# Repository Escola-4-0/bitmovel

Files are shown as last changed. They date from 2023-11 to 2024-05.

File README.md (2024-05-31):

# BitMóvel
Com esta placa você pode fazer um robô controlado pela micro:bit que é fácil de montar e programar com a extensão Escola 4.0 para o MakeCode. A própria placa serve como chassi do robô e dispensa o uso de conectores especiais para a micro:bit. A pasta [bitmovel](https://github.com/Escola-4-0/bitmovel/tree/main/bitmovel) contém o projeto da PCB para o KiCAD e arquivos gerber prontos para fabricação.

As peças `para-choque.stl` e `suporte-sensor.stl` podem ser impressas em 3D para caracterizar seu robô e fixar sensores para fazê-lo funcionar como um seguidor de linha. 

## Características da placa (v3)
- Placa em face simples;
- Componentes em PTH para facilicar a montagem manual;
- Fixação da micro:bit usando parafusos;
- Fornece alimentação regulada 3.3V para a micro:bit;
- CI ponte-h para dois motores DC;
- Permite a conexão de sensores para seguidor de linha.

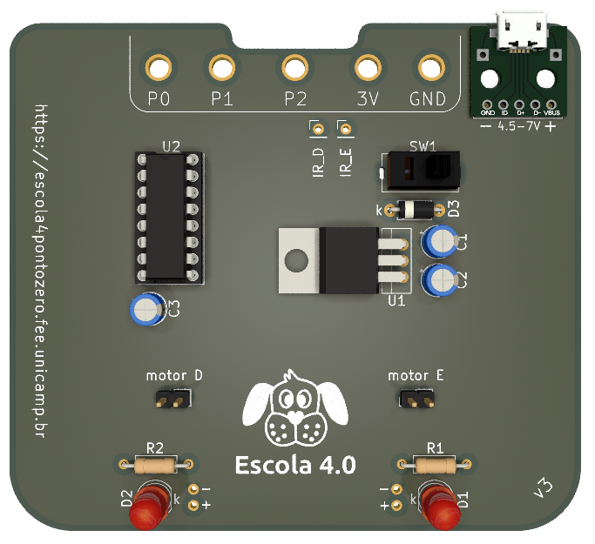
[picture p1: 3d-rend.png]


## Lista de materiais

REF | componente
-- | --
C1 | Capacitor eletrolítico 10uF - 10V |
C2 | Capacitor eletrolítico 10uF - 10V |
C3 | Capacitor eletrolítico 10uF - 10V |
D1 | LED difuso 5mm
D2 | LED difuso 5mm
D3 | Diodo 1N5817 (1N5818 - 1N5822 compatíveis)
J1 | Módulo adaptador micro-USB fêmea para DIP (opcional)
R1 | Resistor 330Ω
R2 | Resistor 330Ω
SW1 | Chave HH SS12F46 - 3 terminais
U1 | LM1117-3.3 (regulador de tensão 3.3V)
U2 | L293D (driver para motor DC)

Para implementar a função de seguidor de linha, são necessários ainda **2 módulos de sensor infravermelho TCRT5000**.

## Descrição e funcionamento
Seis pinos da micro:bit fornecem os sinais de entrada do driver L293D que controla os motores, conforme a tabela: 

pino micro:bit | pino L293D
:--: | :--:
P0 | 2A
P1 | 1A
P2 | 4A
P8 | 1,2EN
P13 | 3A
P15 | 3,4EN

A micro:bit é alimentada pelo regulador LM1117 de 3.3V, o driver L293D e os LEDs são alimentados diretamente pela tensão de entrada, a fonte deve ser de 4.5 a 7V.

Os pinos P14 e P16 recebem os sinais digitais do sensor infravermelho direito e esquerdo, respectivamente.

## Programação
A tabela abaixo resume os comandos para acionamento dos motores:

P8 (P15) | P0 (P2) | P1 (P13) | motor D (motor E)
:--: | :--: | :--: | --
PWM | 1 | 0 | girar horário*
PWM | 0 | 1 | girar anti-horário*
1 | 1 | 1 | parada forçada
1 | 0 | 0 | parada forçada
0 | X | X | parada livre

*O sentido real depende da ligação do motor. X = não importa.

Os sinais dos sensores infravermelho seguem a lógica da tabela abaixo:

P14 (P16) | sensor D (sensor E)
:--: | :--:
0 | luz refletindo, superfície clara
1 | luz não refletindo, superfície escura

No MakeCode, o BitMóvel pode ser programado com os blocos `gravação digital pin` e `gravação analógica pin`, seguindo as combinações da tabela acima, ou com a [extensão Escola 4.0](https://github.com/Escola-4-0/pxt-Escola_4pontozero), usando os blocos da categoria "BitMóvel".

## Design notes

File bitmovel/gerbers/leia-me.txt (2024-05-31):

Cada pasta contém os arquivos em uma versão do formato gerber, X1 ou X2. Verifique com a fabricante qual é o formato compatível.

O projeto contém duas camadas de cobre, mas é possível fabricar a placa em face simples sem perda de funcionalidade, apenas com a camada inferior (bottom layer). Portanto, para fabricar em face simples, ignore os arquivos:
- bitmovel-F_Cu.gbr
- bitmovel-F_Mask.gbr
- bitmovel-F_SilkS.gbr

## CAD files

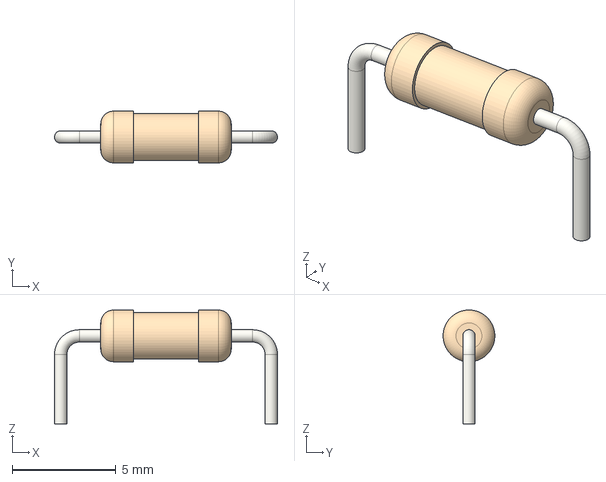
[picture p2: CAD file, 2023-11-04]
bitmovel/3Dmodels/R_Axial_DIN0207_L6.3mm_D2.5mm_P10.16mm_Horizontal.step
10.8 x 2.50 x 5.50 mm

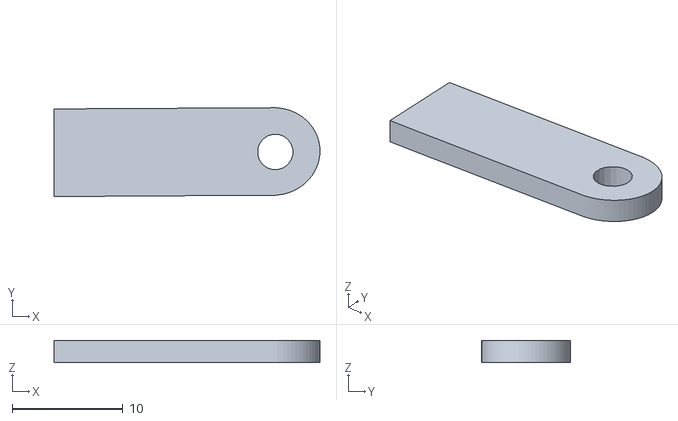
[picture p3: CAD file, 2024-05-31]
suporte-sensor.stl
24.0 x 8.00 x 2.00

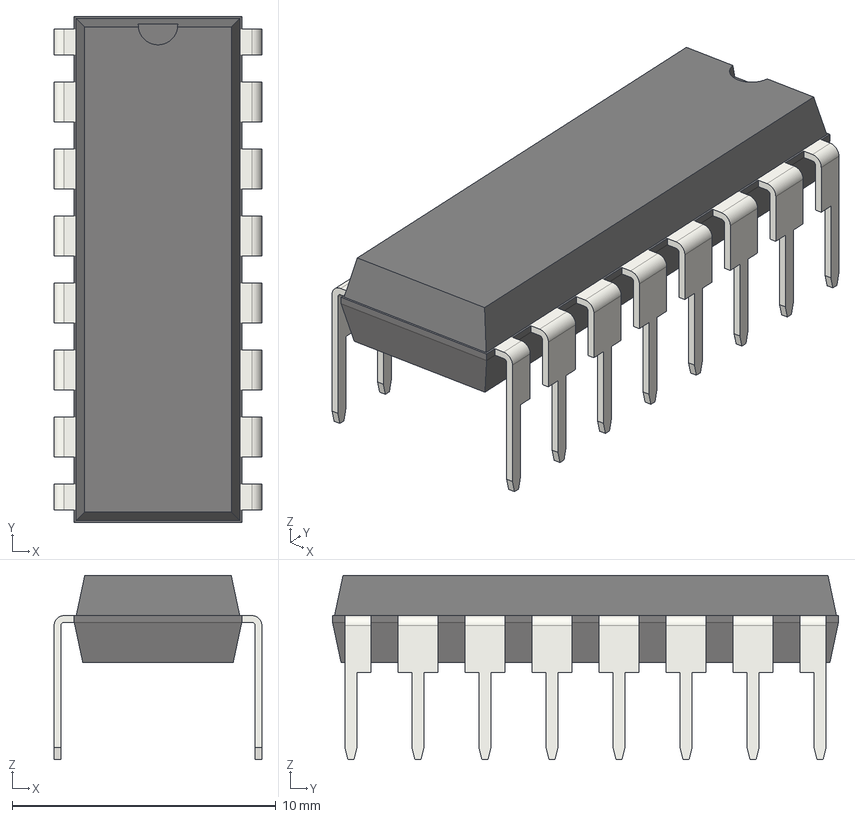
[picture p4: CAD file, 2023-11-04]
bitmovel/3Dmodels/DIP-16_W7.62mm.step
7.87 x 19.2 x 6.98 mm

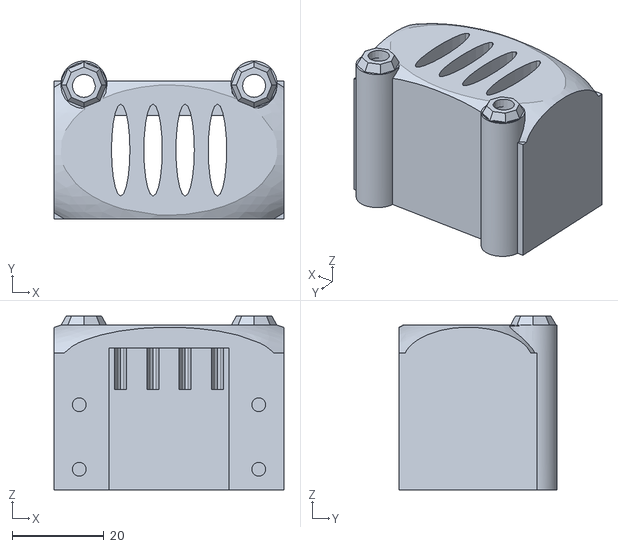
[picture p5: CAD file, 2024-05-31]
para-choque.stl
50.0 x 34.4 x 37.8

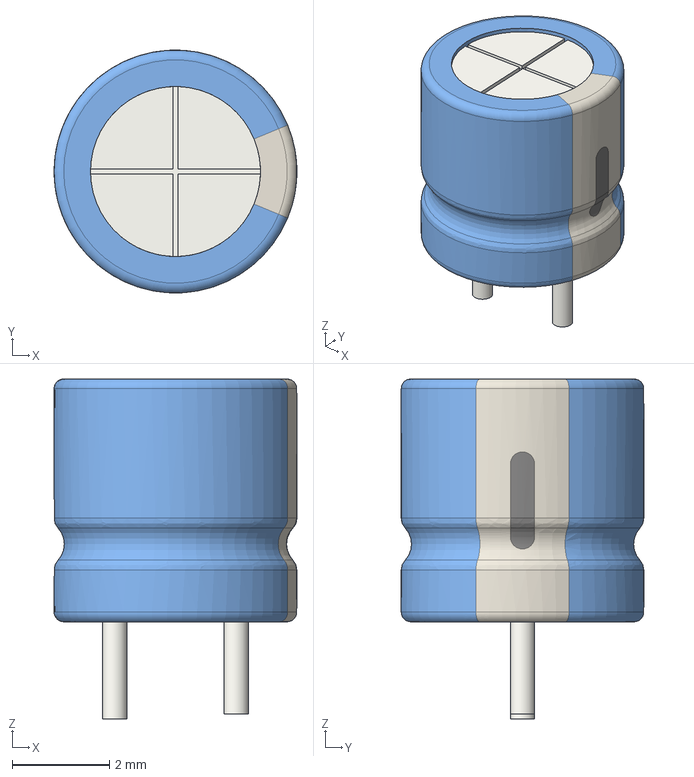
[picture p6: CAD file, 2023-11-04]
bitmovel/3Dmodels/CP_Radial_D5.0mm_P2.50mm.step
5.00 x 5.00 x 7.00 mm

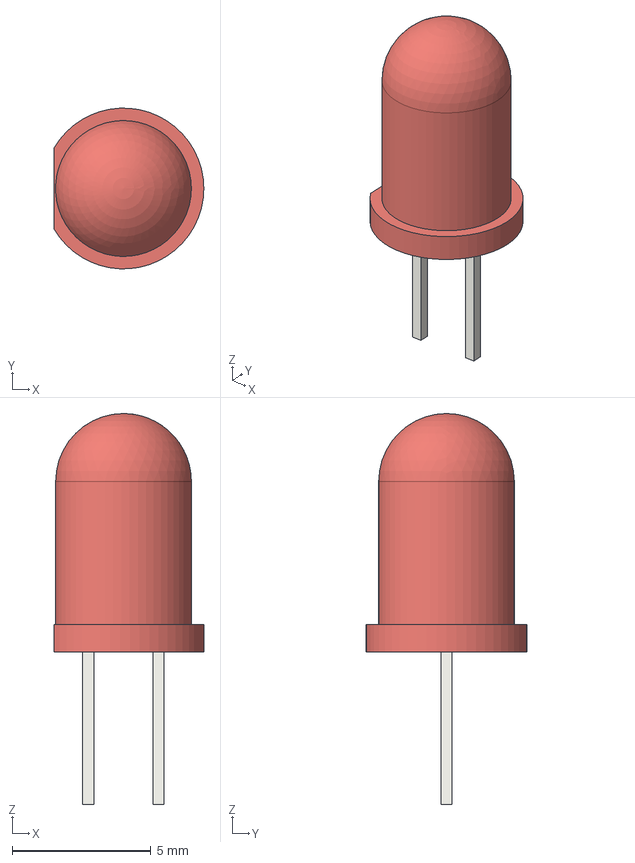
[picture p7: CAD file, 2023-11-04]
bitmovel/3Dmodels/LED_D5.0mm.step
5.40 x 5.79 x 14.1 mm

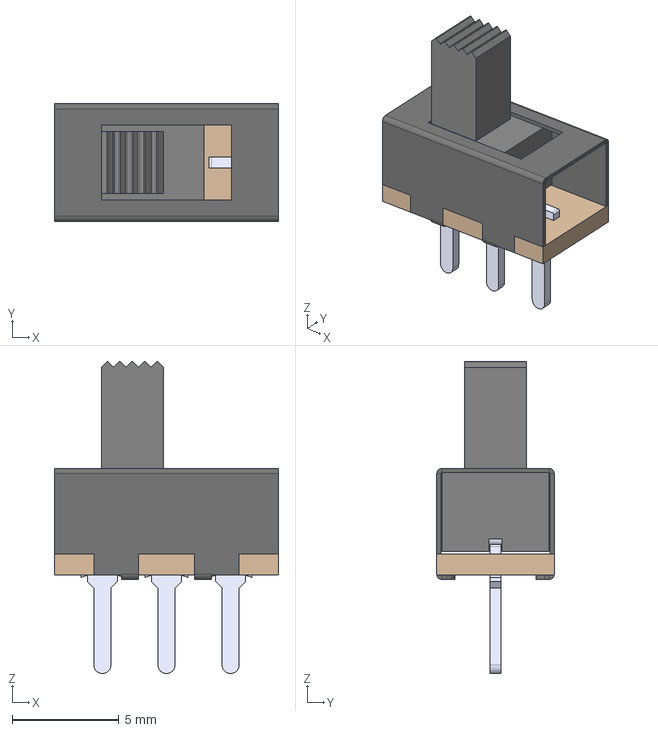
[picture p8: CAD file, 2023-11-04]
bitmovel/3Dmodels/slide_switch.step
10.5 x 5.50 x 14.6 mm

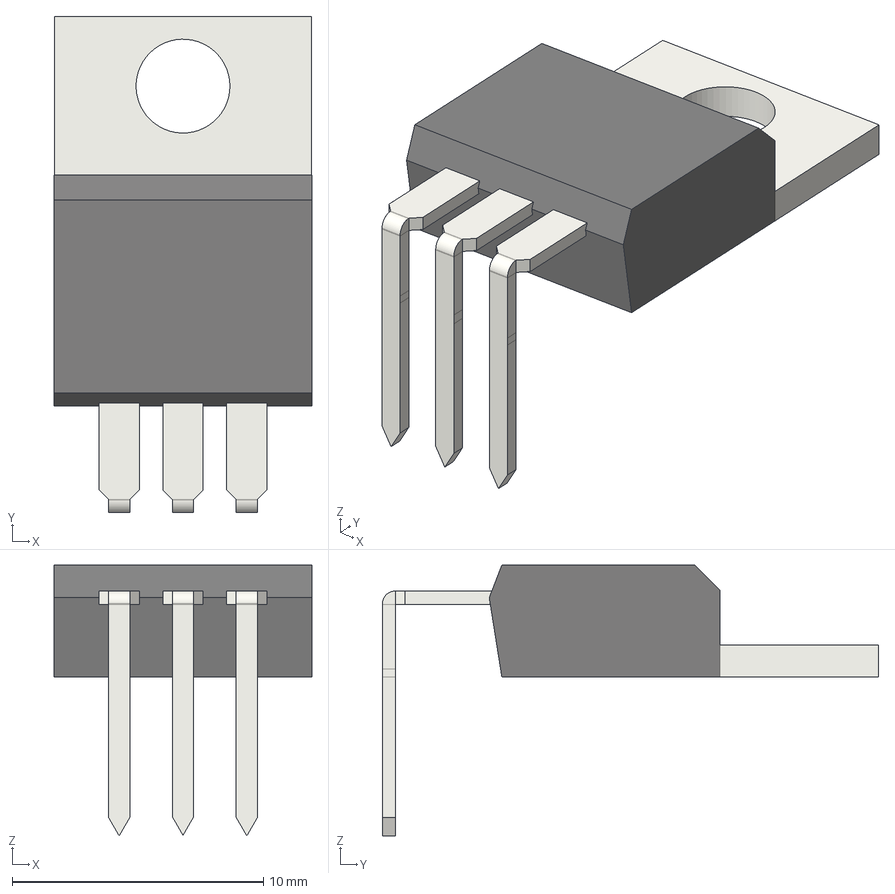
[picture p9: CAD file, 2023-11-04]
bitmovel/3Dmodels/TO-220-3_Horizontal_TabDown.step
10.2 x 19.7 x 10.8 mm

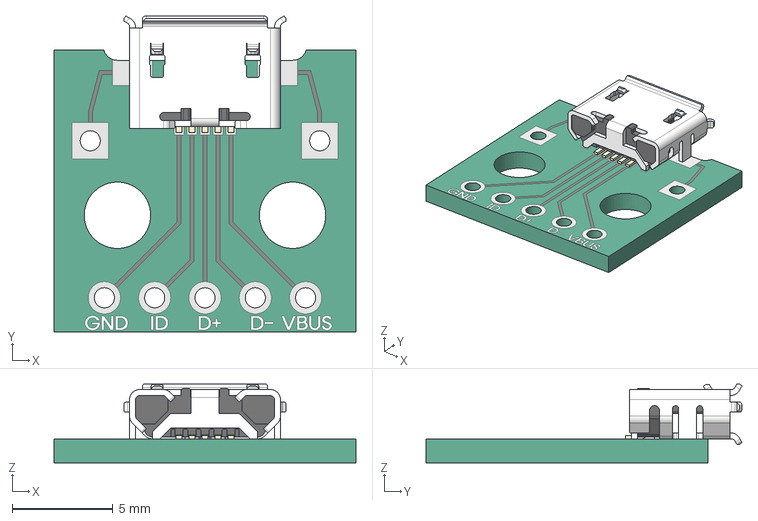
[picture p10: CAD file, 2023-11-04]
bitmovel/3Dmodels/USB-5pin-board.step
15.0 x 15.7 x 3.92 mm

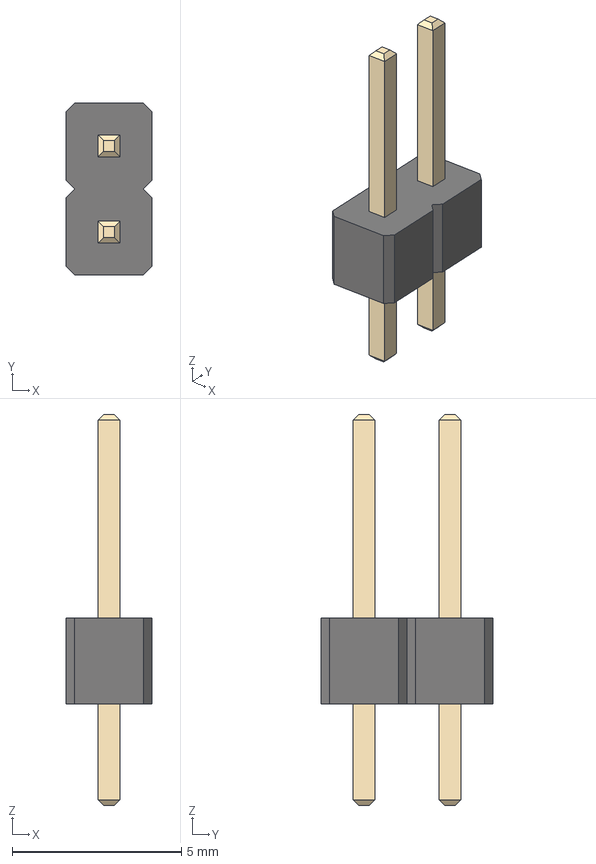
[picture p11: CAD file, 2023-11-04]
bitmovel/3Dmodels/PinHeader_1x02_P2.54mm_Vertical.step
2.54 x 5.08 x 11.5 mm

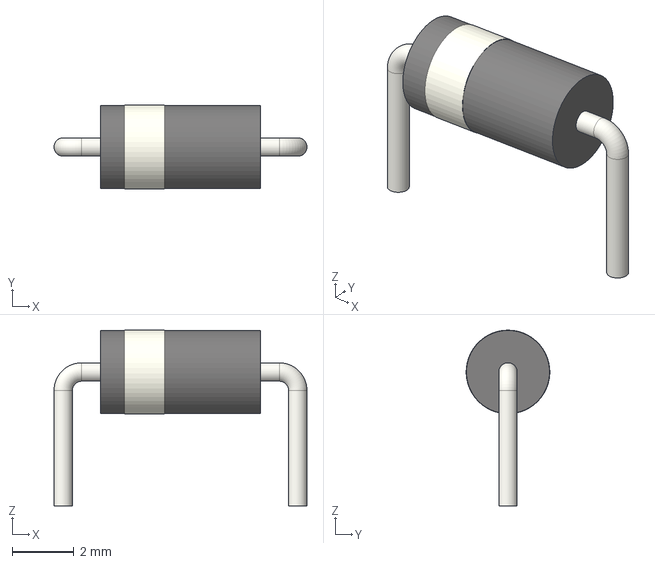
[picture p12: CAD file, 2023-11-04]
bitmovel/3Dmodels/D_A-405_P7.62mm_Horizontal.step
8.22 x 2.72 x 5.71 mm

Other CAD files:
bitmovel/3Dmodels/REAL-Usb 5pin Board.STEP

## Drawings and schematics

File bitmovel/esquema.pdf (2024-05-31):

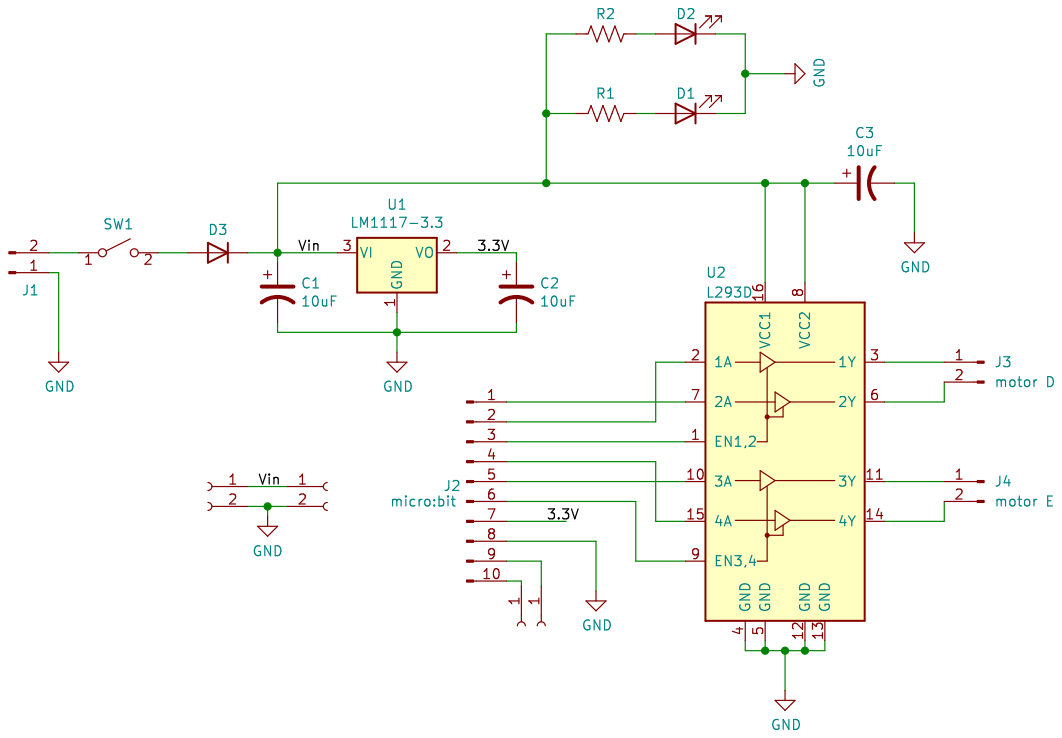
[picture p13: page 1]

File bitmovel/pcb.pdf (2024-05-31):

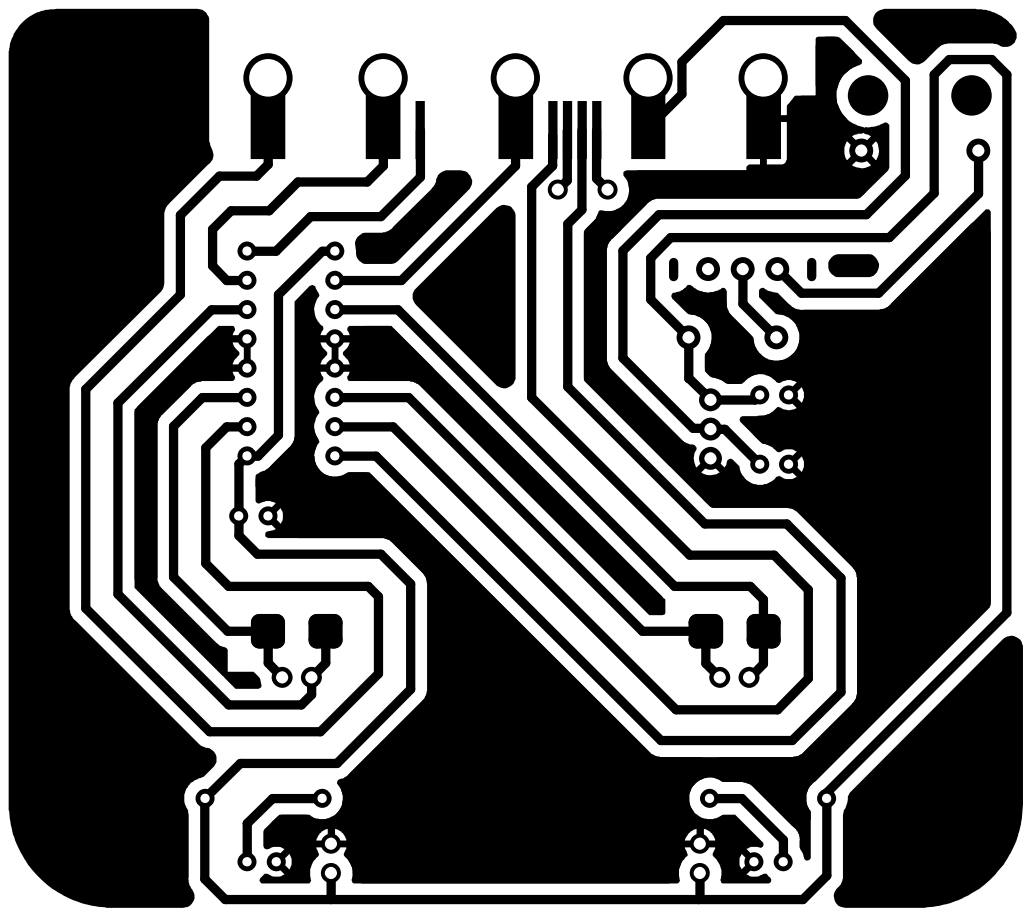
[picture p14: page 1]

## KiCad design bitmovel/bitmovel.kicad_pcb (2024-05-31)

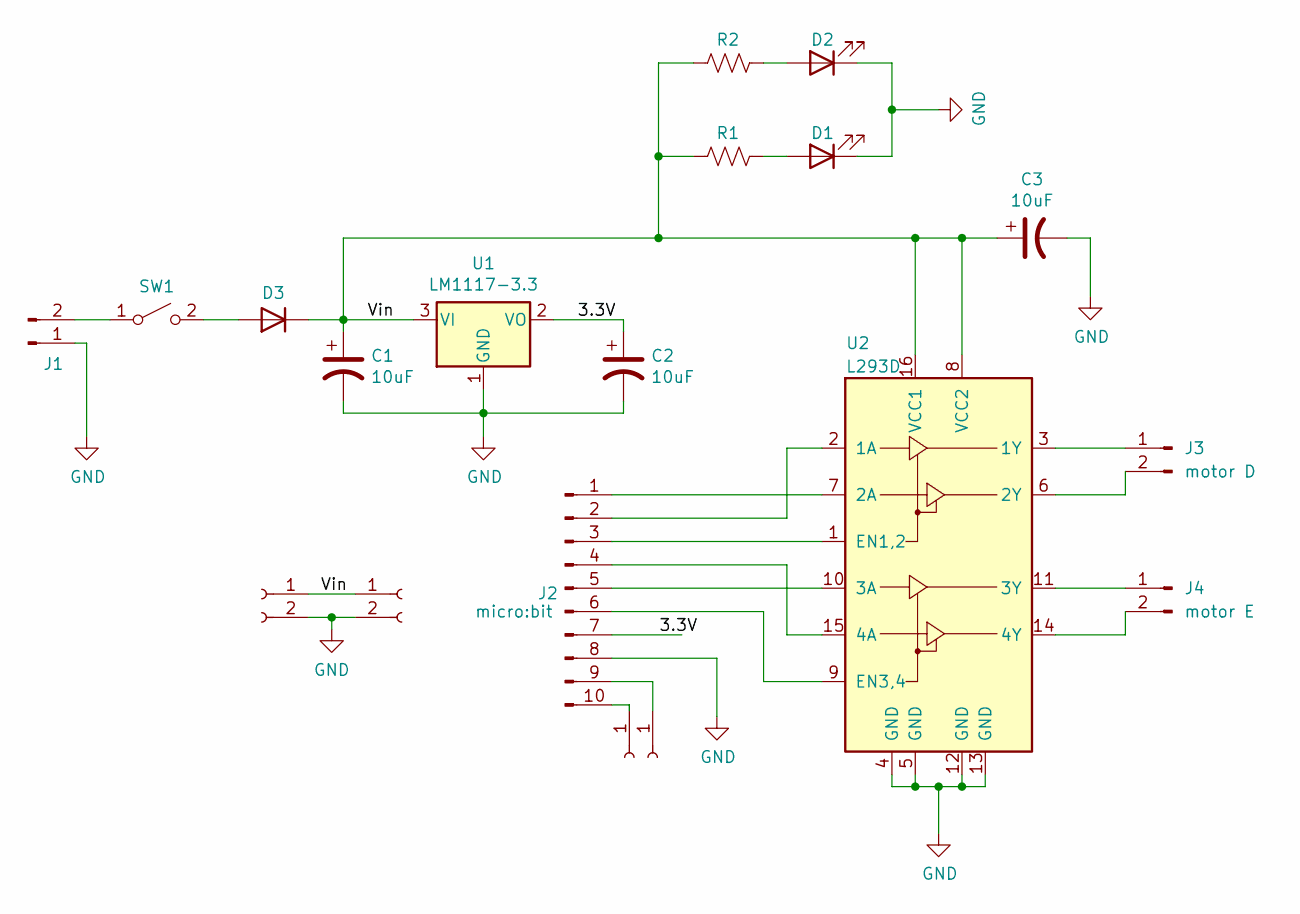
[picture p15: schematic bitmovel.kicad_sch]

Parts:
C1, C2, C3: 10uF; CP_Radial_D5.0mm_P2.50mm
D1, D2: LED; LED_D5.0mm
D3: D_Small; D_A-405_P7.62mm_Horizontal
J1: Conn_01x02_Male; microUSB-breakout-2pin
J2: micro:bit; microbit_edge_rings
J3: motor D; SolderJumper-2_P1.3mm_Open_RoundedPad1.0x1.5mm
J4: motor E; SolderJumper-2_P1.3mm_Open_RoundedPad1.0x1.5mm
J6, J9: Conn_01x02_Female; PinHeader_1x02_P2.54mm_Vertical
J7, J8: Conn_01x01_Female; PinHeader_1x01_P2.54mm_Vertical
R1, R2: R_US; R_Axial_DIN0207_L6.3mm_D2.5mm_P10.16mm_Horizontal
SW1: SW_SPST; Slide_Switch
U1: LM1117-3.3; TO-220-3_Vertical
U2: L293D; DIP-16_W7.62mm_Socket

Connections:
/3.3V: C2.1, J2.7, U1.2 (VO)
/Vin: C1.1, C3.1, D3.1 (K), J6.1, J9.1, R1.1, R2.1, U1.3 (VI), U2.8 (VCC2), U2.16 (VCC1)
GND: C1.2, C2.2, C3.2, D1.1 (K), D2.1 (K), J1.1, J2.8, J6.2, J9.2, U1.1 (GND), U2.4 (GND), U2.5 (GND), U2.12 (GND), U2.13 (GND)
unnamed: D1.2 (A), R1.2
unnamed: D2.2 (A), R2.2
unnamed: D3.2 (A), SW1.2 (B)
unnamed: J1.2, SW1.1 (A)
unnamed: J2.1, U2.7 (2A)
unnamed: J2.2, U2.2 (1A)
unnamed: J2.3, U2.1 (EN1,2)
unnamed: J2.4, U2.15 (4A)
unnamed: J2.5, U2.10 (3A)
unnamed: J2.6, U2.9 (EN3,4)
unnamed: J2.9, J8.1
unnamed: J2.10, J7.1
unnamed: J3.1, U2.3 (1Y)
unnamed: J3.2, U2.6 (2Y)
unnamed: J4.1, U2.11 (3Y)
unnamed: J4.2, U2.14 (4Y)

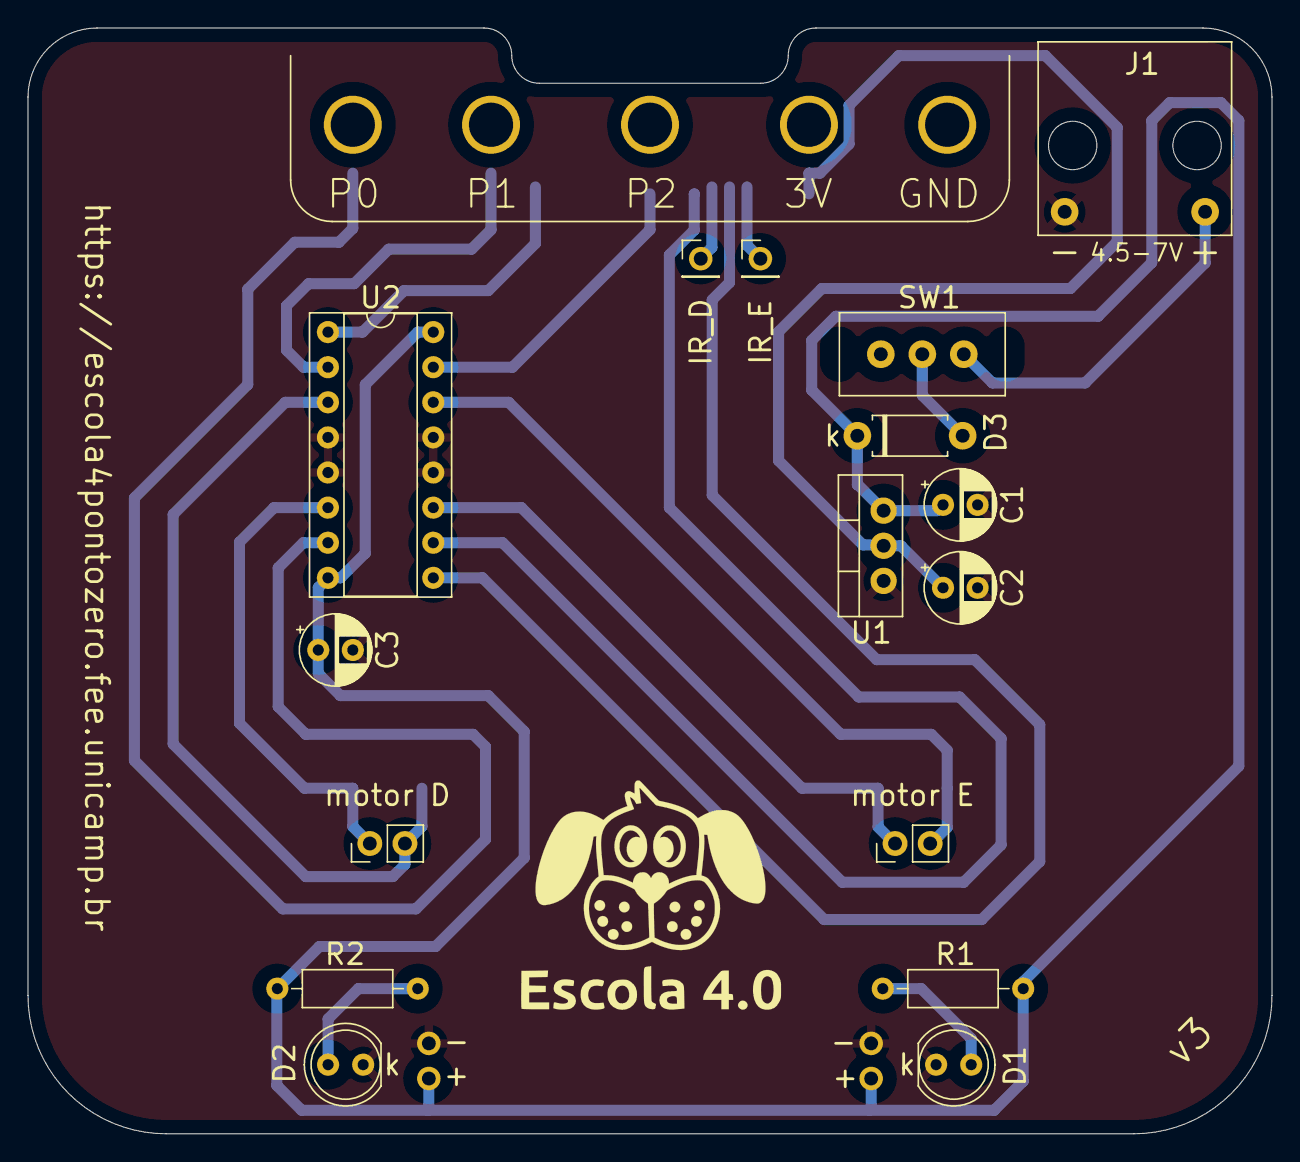
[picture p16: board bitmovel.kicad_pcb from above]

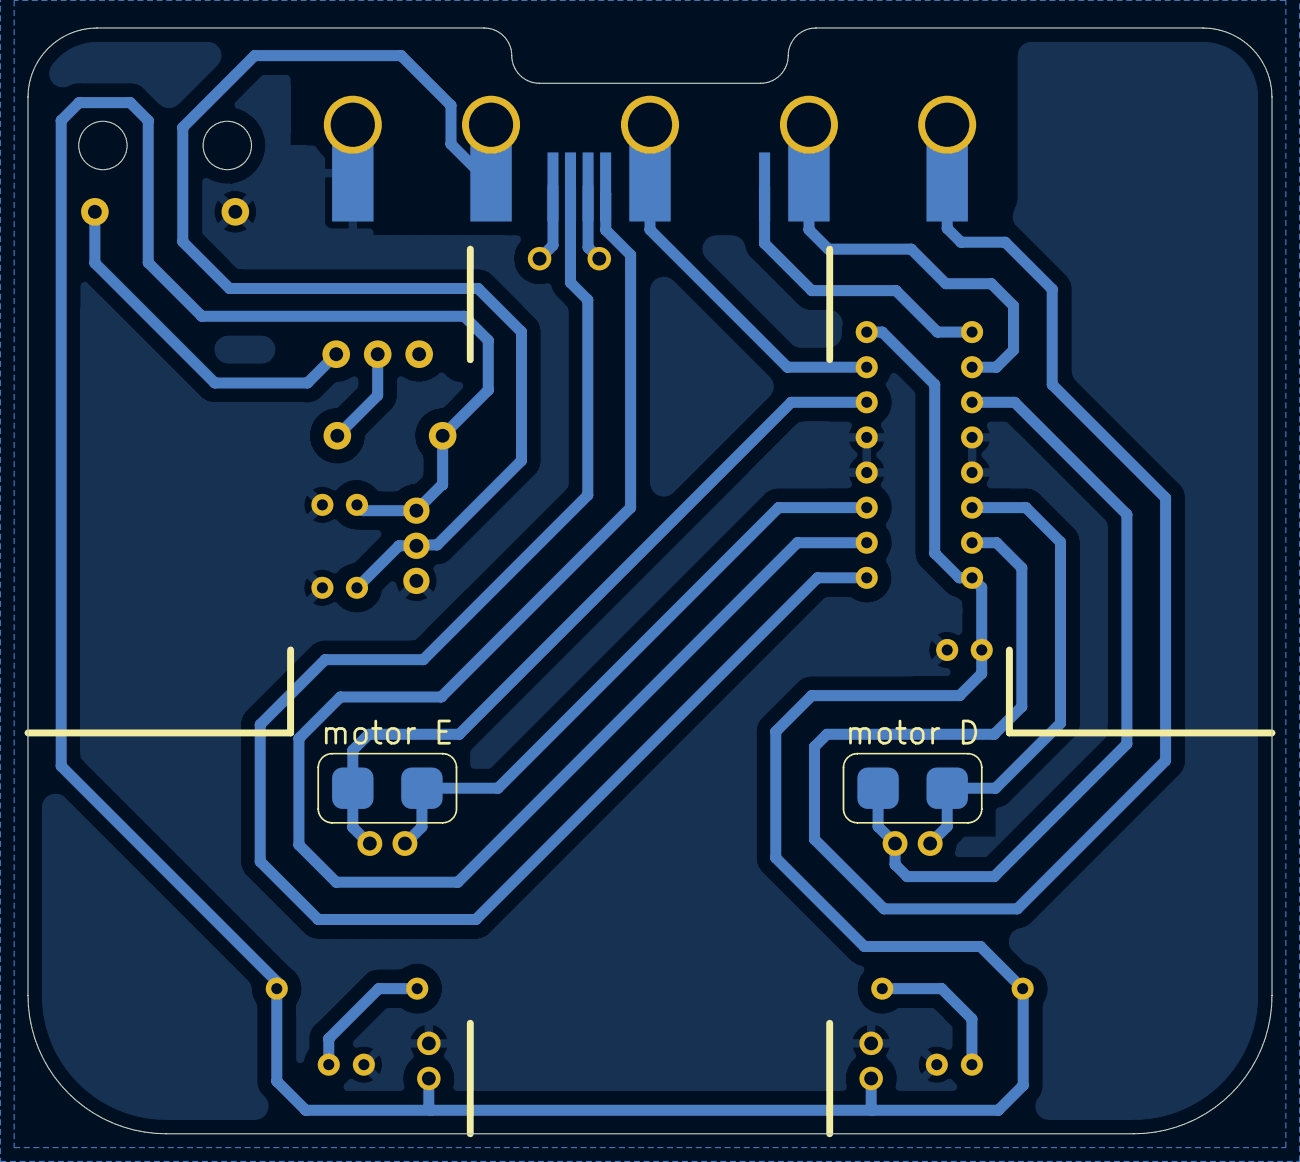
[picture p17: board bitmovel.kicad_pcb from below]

Board: 2 copper layers, 90.0 x 80.0 mm, 19 parts (2 on the bottom side), 19 nets.

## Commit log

2023-11-04 Atualizando URL e versão da placa impressas na silkscreen
    [CP_Radial_D5.0mm_P2.50mm.step, DIP-16_W7.62mm.step, D_A-405_P7.62mm_Horizontal.step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]
2023-11-05 atualizando arquivos gerber
    [bitmovel-B_Cu.gbr, bitmovel-B_Mask.gbr, bitmovel-B_SilkS.gbr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]
2024-03-05 Adiciona pads P14 e P16 no footprint da microbit
2024-03-05 Inclui ilhas para conectar P14, P16, 3V3 e GND
    [bitmovel.kicad_pcb, bitmovel.kicad_sch]
2024-03-06 Inclui ilhas para conectar a Vin
    [bitmovel.kicad_pcb, bitmovel.kicad_sch]
2024-03-09 Remove arquivos legados
    [bitmovel.sch]
2024-03-09 Corrige posição das ilhas 3v3 e GND
    [bitmovel.kicad_pcb, bitmovel.kicad_sch]
2024-03-11 Atualiza gerbers
    [bitmovel-B_Cu.gbr, bitmovel-B_Mask.gbr, bitmovel-B_Silkscreen.gbr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]
2024-05-31 Atualiza versão para v3 e outros ajustes na silkscreen
    [bitmovel.kicad_pcb]
2024-05-31 Atualiza gerbers com número de versão
    [bitmovel-B_Cu.gbr, bitmovel-B_Mask.gbr, bitmovel-B_Silkscreen.gbr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]
2024-05-31 Inclui peças para impressão 3D
    [para-choque.stl, suporte-sensor.stl]
2024-05-31 Corrige arquivo 3D do suporte do sensor
    [suporte-sensor.stl]

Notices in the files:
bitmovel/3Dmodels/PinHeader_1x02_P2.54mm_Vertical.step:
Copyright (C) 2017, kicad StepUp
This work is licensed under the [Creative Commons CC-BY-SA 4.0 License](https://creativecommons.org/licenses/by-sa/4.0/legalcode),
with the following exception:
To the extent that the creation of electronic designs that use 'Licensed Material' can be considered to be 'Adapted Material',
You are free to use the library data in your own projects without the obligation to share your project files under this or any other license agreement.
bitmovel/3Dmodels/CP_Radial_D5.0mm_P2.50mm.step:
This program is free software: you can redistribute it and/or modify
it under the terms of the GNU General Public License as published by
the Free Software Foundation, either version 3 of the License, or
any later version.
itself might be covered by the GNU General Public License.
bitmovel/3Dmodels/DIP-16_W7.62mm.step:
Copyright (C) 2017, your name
